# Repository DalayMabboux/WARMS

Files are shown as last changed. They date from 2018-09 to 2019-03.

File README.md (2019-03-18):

# WARMS
> Automatic plant watering with remote control and luminance, temperature and humidity data logging

Measures the moisture levels with two sensors and waters the plants individually.
The values are transmitted from the ESP8266 over MQTT to Node-RED, If the moisture level is too low the ESP8266 will be instructed to switch on the micro water pumps.

WARMS (http://www.youtube.com/watch?v=PIqeCujVt_k "WARMS")

## Overview
The whole installation consists of the following parts:
1. A Raspberry PI running Mosquitto (MQTT server) and Node-RED
2. A sensor box made up from a ESP8266, some sensors, micro pumps, etc.
3. A cloud based (GKE Google Kubernetes Engin) watchdog. If the cloud 'alive' doesn't get a callback from Node-RED, then an email will be sent . If the cloud 'alive' doesn't get a callback from Node-RED, then an email ("Alert, no heartbeat recevied from WARMS") will be sent.

## Raspberry PI
### SSL certificate
As the sensor data and the modification of the watering trigger value should easily be changeable, the Node-RED UI will be reachable over the Internet.
And secure it accordingly we'll enable HTTPS.
With the free service from [Let’s Encrypt](https://letsencrypt.org/) this is an easy task.
1) Get a certificate for madalito.internet-box.ch: `sudo certbot certonly --standalone --preferred-challenges http-01 -d madalito.internet-box.ch`
   * Hint: Create a cron job trying every hour to get a certificate
   
1) Also add a cron job to renew the certificate: `0 3 * * 6 certbot renew --noninteractive --standalone --post-hook "systemctl restart mosquitto"`

See [here](https://www.digitalocean.com/community/tutorials/how-to-install-and-secure-the-mosquitto-mqtt-messaging-broker-on-ubuntu-16-04) for a good info page.

### Node-RED
1) Follow the installation instruction on the [Node-RED site (Raspberry PI)](https://nodered.org/docs/hardware/raspberrypi).
1) Install [node-red-dashboard](https://github.com/node-red/node-red-dashboard)
1) Copy / paste [this](code/NodeRED.json)

#### Dashboard
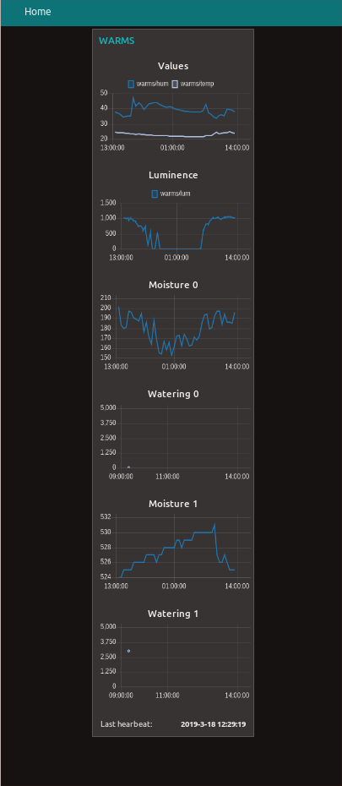
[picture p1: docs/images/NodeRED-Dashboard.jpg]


### Mosquitto
1) Install mosquitto
1) Configure mosquitto:
   - Don't allow anonymous access
   - Specify the location of the SSL certificate
   - Configuration: [default.conf](code/default.conf) [mosquitto.conf](code/mosquitto.conf)
1) Restart: `sudo systemctl restart mosquitto`

## Sensor box
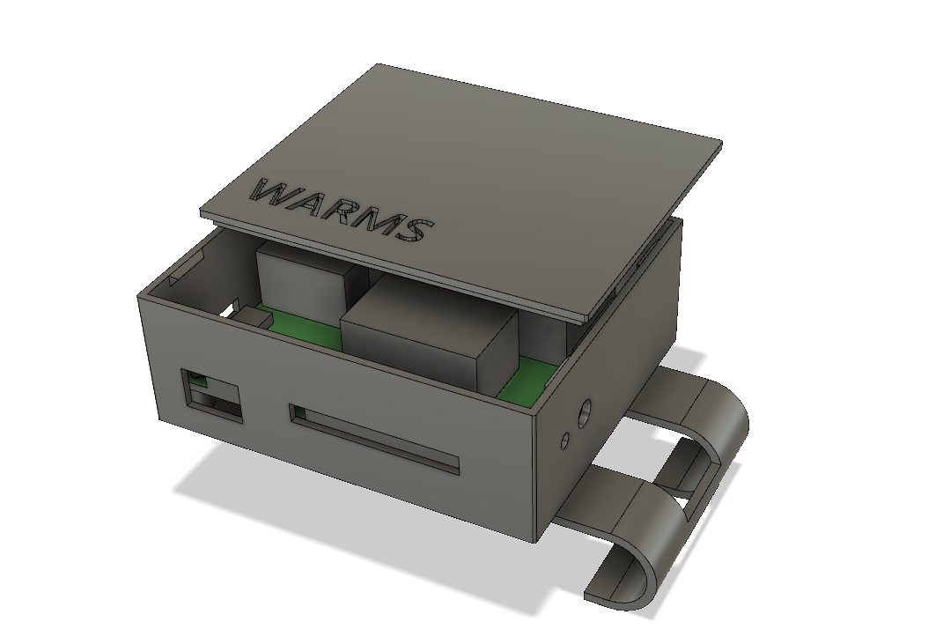
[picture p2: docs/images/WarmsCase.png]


### Printed circuit
For the first prototype I used an `Arduino Nano` and an ESP8266 to connect to the Internet. The Arduino was wired to the ESP8266 by a software serial connection. I wasn't able to build a reliable link between the two. So I dropped the Arduino an used just the ESP8266. The only issue with this approach was, that the ESP8266 (ESP-01) didn't have enough IO ports (one less I needed) available.
Fortunately there is a [solution](https://www.instructables.com/id/More-GPIO-for-ESP8266-01/) to this problem :)

[JLCPCB](https://jlcpcb.com) printed 10 of them for 2$ (exclusive shipping costs).

#### Schema
The schema has been drawn in [Autodesk EAGLE](https://www.autodesk.com/products/eagle/overview).

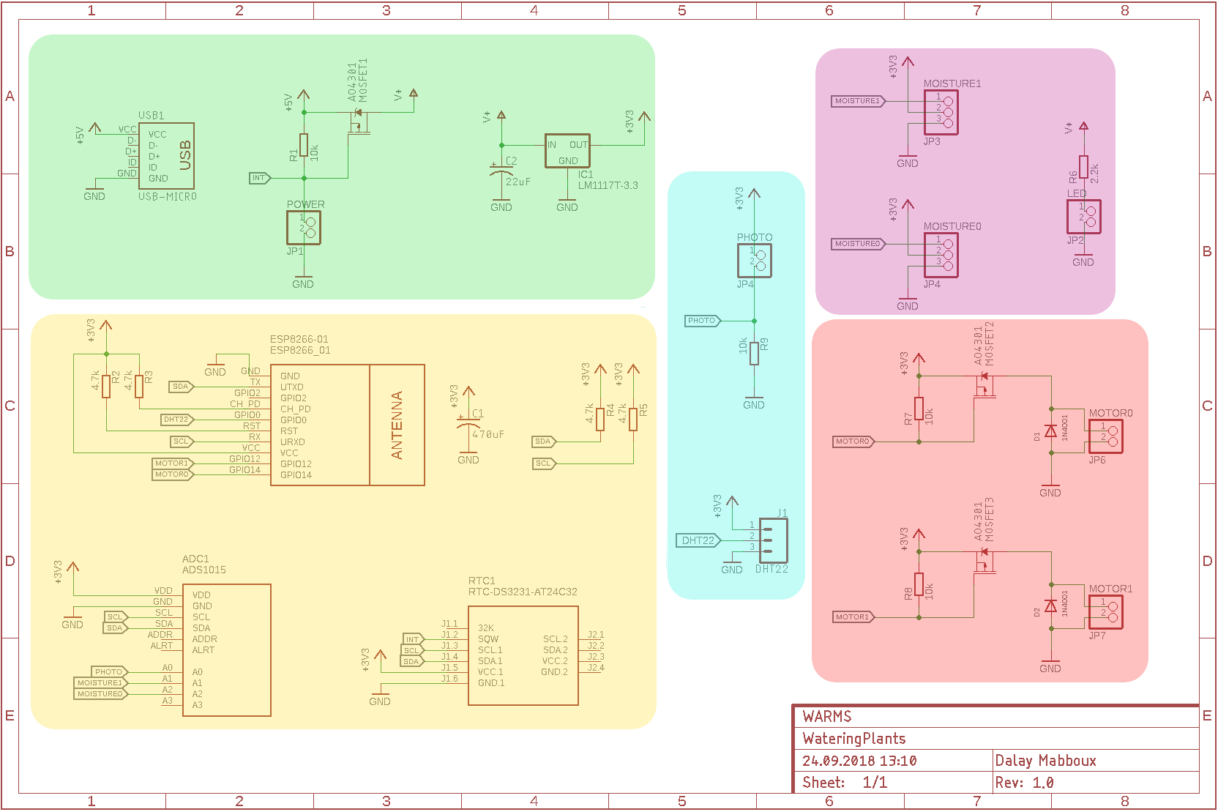
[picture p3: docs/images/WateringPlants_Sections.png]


It is grouped into these sectios:
Color | Section | Remark
--- | --- | ---
Green | Power supply | USB connector, 5V to 3.3V converter and switching circuit
Yellow | Micro-controller and sensor circuits | 
Blue | Sensor connectors | Moisture, luminance, etc
Purple | Green power led | Switches on once the device is running
Red | Water pump driver |

> The device will be powered off until the DS3231 switches SQW low (interrupt output). This happens when a set alarm occurs (currently it is set to 30min).
> If `INT` is low then VGS will be greater than VGS threshold and the P-Channel MOSFET turns on. Then the voltage on V+ will be ~5V and with LM 1117T-3.3 will output 3.3V. The ESP8266 boots and starts the sketch (todo: see).

##### Power supply (green)
Most of the functionality has already been described in the paragraph above.

The POWER jumper JP1 is used to manually boot the device. Needed, when you first start the board (as no alarm is set at this time).

##### Micro controller and sensor circuits (yellow)
The Real-Time-Clock (RTC-DS3231) and the Analog-to-Digital converter (ADS1015) are connected to the ESP8266 by I2C.

C1 is used as decoupling capacitor (I really had weird phenomenon without it).

As the ESP8266-01 just has 2 GPIO's (GPIO 0 and GPIO 2) and these have special purpose functionality while the the micro controller starts. I decided to wire out GPIO 12 and GPIO 14 to get some extra unused pins. If I didn't already have these boards I would by another version of the ESP8266 (ex. ESP-07) to circumvent the tinkering / soldering (see [here](https://www.instructables.com/id/More-GPIO-for-ESP8266-01/) how to do it).

The WARMS board just uses 3 (A0 to A3) of the 4 AD inputs of the ADS1015.

##### Water pump driver (red)
MOTOR0 and MOTOR1 will be set to GND to switch on the P-channel MOSFETS.

The diodes (D1 and D2) are just Flyback-Diodes.

#### Arduino sketch
The sketch first sets all parts up (I2C, RTC, Wifi, MQTT, IN-OUTPUT). Then the main loop starts by connecting to MQTT (subscribe for PUMP and SLEEP messages). The SLEEP functionallity hasn't yet been implemented.
Once all is set up, then it starts transmitting the luminence, moisture 1 and 2, humidity and temparture.

### 3D printed parts
All parts have been drawn with [Autodesk Fusion 360](https://www.autodesk.com/products/fusion-360/overview).
The Fusion Archive file can be found [here](code/WARMS_Box.f3d).

## Meta
Dalay Mabboux – [@mabbouxd](https://twitter.com/mabbouxd)

WARMS is licensed under a
Creative Commons Attribution-ShareAlike 4.0 International License.

You should have received a copy of the license along with this
work. If not, see <http://creativecommons.org/licenses/by-sa/4.0/>.

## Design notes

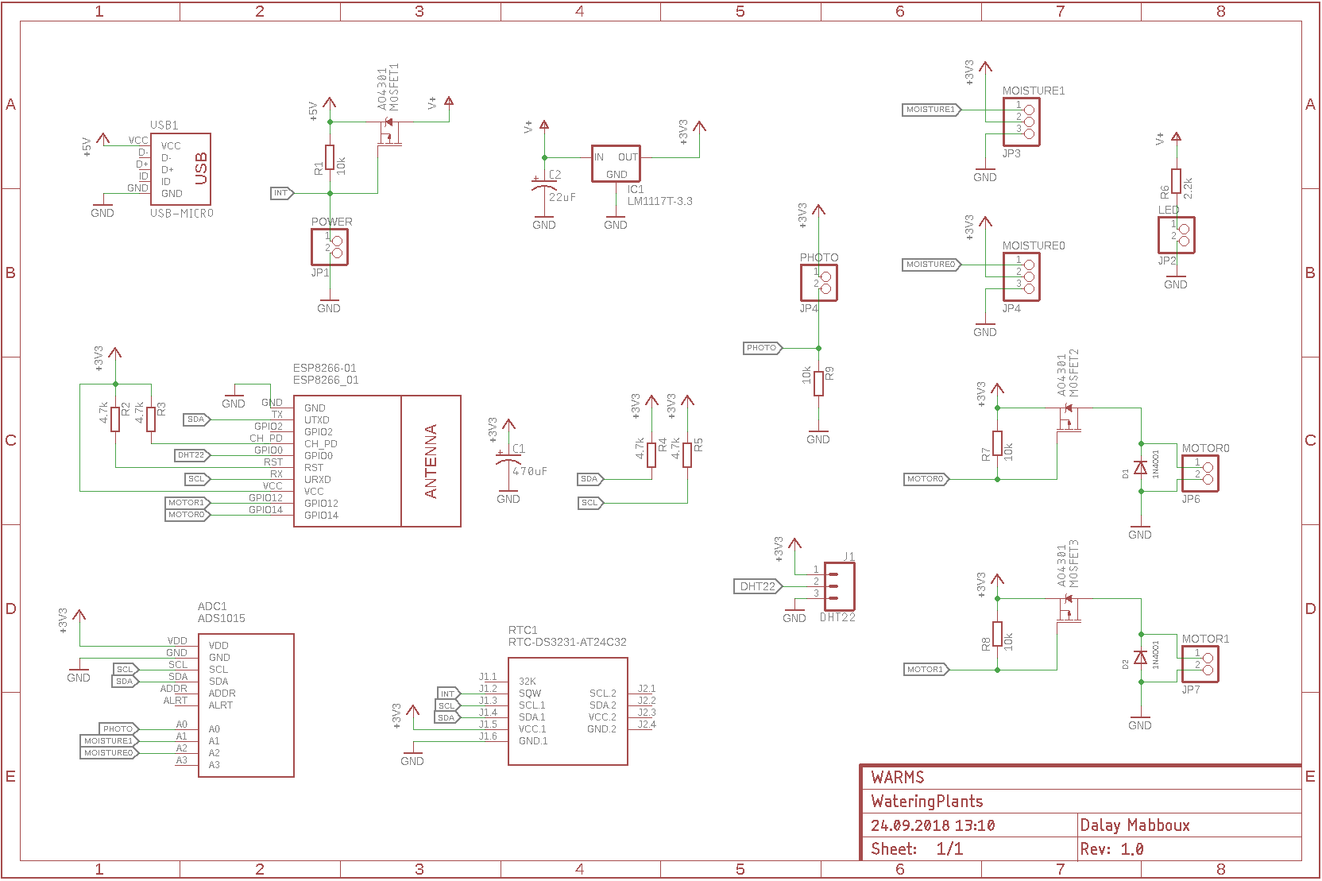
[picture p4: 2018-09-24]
docs/images/WateringPlants.png

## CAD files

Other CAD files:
code/WARMS_Box.f3d

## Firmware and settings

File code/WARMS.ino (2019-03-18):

/*
WARMS (c) by Dalay Mabboux

WARMS is licensed under a
Creative Commons Attribution-ShareAlike 4.0 International License.

You should have received a copy of the license along with this
work. If not, see <http://creativecommons.org/licenses/by-sa/4.0/>.
*/

#include <ESP8266WiFi.h>
#include <ESP8266WiFiMulti.h>
#include <PubSubClient.h>
#include <Wire.h> // must be included here so that Arduino library object file references work
#include <RtcDS3231.h>
#include <Adafruit_ADS1015.h>
#include "DHT.h"

// GPIO
const short int DHTPIN = 0; // GPIO0
const short int PUMP0 = 14; //GPIO14
const short int PUMP1 = 12; //GPIO12

// DIV
short int LL = 2; // Log level: 2 = debug, 1 = info, 0 = failure
short int sleepDuration = 1800; // Measurement period, default = 30min = 1800s
bool callbackHandled = false;

// MQTT
const char MQTT_SERVER[] =    "1.1.1.1";
const int MQTT_SERVERPORT =   1883;
const char MQTT_USERNAME[] =  "warms";
const char MQTT_PASSWORD[] =  "xxxxxxxxxx";
const char* MQTT_USERID;

// Feeds
const char MQTT_FEED_LOG[] =  "warms/log";
const char MQTT_FEED_TEMP[] = "warms/temp";
const char MQTT_FEED_HUM[] =  "warms/hum";
const char MQTT_FEED_LUM[] =  "warms/lum";
const char MQTT_FEED_MOI0[] = "warms/moi0";
const char MQTT_FEED_MOI1[] = "warms/moi1";
// Subscriptions
const char MQTT_SUB_PUMPS[] = "warms/pumps";
const char MQTT_SUB_SLEEP[] = "warms/sleepDuration";

// WIFI
const char WIFI_SSID[] = "xxxxxxxxxx";
const char WIFI_PASSWORD[] = "xxxxxxxxxx";
ESP8266WiFiMulti WiFiMulti;
WiFiClient wclient;
PubSubClient mqttclient(wclient);

// AD-Converter
Adafruit_ADS1015 ads;

// RTC
RtcDS3231<TwoWire> rtc(Wire);
#define countof(a) (sizeof(a) / sizeof(a[0]))

// DHT
const uint8_t DHTTYPE = DHT22;
DHT dht(DHTPIN, DHTTYPE);

struct PUMP_DURATIONS {
  unsigned int p0;
  unsigned int p1;
};

PUMP_DURATIONS calcPumpDurations(byte* payload);


/* SETUP ************************************************************************************************/
void setup() {
  Wire.begin(1, 3);
  rtc.Begin();
  rtc.Enable32kHzPin(false);
  rtc.SetSquareWavePin(DS3231SquareWavePin_ModeAlarmOne);
  ads.begin();
  dht.begin();

  RtcDateTime compiled = RtcDateTime(__DATE__, __TIME__);
  RtcDateTime now = rtc.GetDateTime();
  rtc.SetDateTime(compiled);

  if (!rtc.GetIsRunning()) {
    rtc.SetIsRunning(true);
  }

  // WIFI
  WiFi.mode(WIFI_STA);
  WiFiMulti.addAP(WIFI_SSID, WIFI_PASSWORD);
  while (WiFiMulti.run() != WL_CONNECTED) { // Wait until WIFI has been connected
    delay(500);
  }

  // MQTT
  String clientId = "ESP8266Client-";
  clientId += String(random(0xffff), HEX);
  MQTT_USERID = clientId.c_str();
  mqttclient.setServer(MQTT_SERVER, 1883);
  mqttclient.setCallback(callback);

  // PINMODES
  pinMode(PUMP0, OUTPUT);
  digitalWrite(PUMP0, HIGH);
  pinMode(PUMP1, OUTPUT);
  digitalWrite(PUMP1, HIGH);
}

/* LOOP ************************************************************************************************/
void loop() {
  if (!mqttclient.connected()) {
    if (mqttclient.connect(MQTT_USERID, MQTT_USERNAME, MQTT_PASSWORD)) {
      mqttclient.subscribe(MQTT_SUB_PUMPS);
      mqttclient.subscribe(MQTT_SUB_SLEEP);
    }
  }
  
  if (!callbackHandled) {
    if (mqttclient.connected()) {
      // Check RTC
      if (!rtc.IsDateTimeValid()) {
        log2mqtt(0, "RTC date/time is not valid (IsDateTimeValid() == false");
      }
      if (!rtc.GetIsRunning()) {
        log2mqtt(0, "RTC was not actively running, starting now");
        rtc.SetIsRunning(true);
      } 
  
      // Handle moisture 1 sensor
      int16_t adc0 = ads.readADC_SingleEnded(0);
      publishFloat(MQTT_FEED_LUM, (float)adc0);
  
      // Handle moisture 2 sensor
      int16_t adc1 = ads.readADC_SingleEnded(1);
      publishFloat(MQTT_FEED_MOI0, (float)adc1);
  
      // Handle light sensor
      int16_t adc2 = ads.readADC_SingleEnded(2);
      publishFloat(MQTT_FEED_MOI1, (float)adc2);
  
      // DHT
      float dhtTemp = dht.readTemperature();
      float dhtHum = dht.readHumidity();
      publishFloat(MQTT_FEED_HUM, dhtHum);
      publishFloat(MQTT_FEED_TEMP, dhtTemp);
  
      // Wait one minute in total for a callback
      int mqttLoops = 12;
      while(mqttLoops >= 0) {
        mqttclient.loop();
        delay(5000);
        --mqttLoops;
      }
    }
  }
  
  // Set alarm
  RtcDateTime now = rtc.GetDateTime();
  RtcDateTime alarmTime = now + sleepDuration;
  DS3231AlarmOne alarm1(alarmTime.Day(), alarmTime.Hour(), alarmTime.Minute(), alarmTime.Second(), DS3231AlarmOneControl_HoursMinutesSecondsMatch);
  char tmpString[150];
  sprintf(tmpString, "Alarm set: %u-%u-%u %u:%u:%u", alarmTime.Year(), alarmTime.Month(), alarmTime.Day(), alarmTime.Hour(), alarmTime.Minute(), alarmTime.Second());
  log2mqtt(2, tmpString);
  // Wait a couple of seconds to send the log entry
  delay(5000);
  rtc.SetAlarmOne(alarm1);
  // Next command will power off the board
  rtc.LatchAlarmsTriggeredFlags();
}

/*
  Publishes the given string to the log feed if the specified loglevel is lower or equal to the log level (LL).
  Max. string size = 80 characters.
  ------------------------------------------------------------------------------------------------------------
    l:    the log level
    m:    the string to send to the log feed

    returns: void
*/
void log2mqtt(short int l, char m[]) {
  if (l <= LL) {
    mqttclient.publish(MQTT_FEED_LOG, m);
  }
}

/* Publishes the float val to the given topic. Format: YYY.YY */
void publishFloat(char const topic[], float val) {
  char tmp[7];
  dtostrf(val, 5, 2, tmp);
  mqttclient.publish(topic, tmp);
}

/* Called when receiving a message from MQTT broker */
void callback(char* topic, byte* payload, unsigned int length) {
  // In order to republish this payload, a copy must be made
  // as the orignal payload buffer will be overwritten whilst
  // constructing the PUBLISH packet.
  byte* p = (byte*) malloc(length);
  memcpy(p, payload, length);

  char tmpString[150];
  sprintf(tmpString, "Received message for the topic '%s' with the payload '%s'", topic, p);
  log2mqtt(2, tmpString);
  
  if (strcmp(topic, MQTT_SUB_SLEEP) == 0) {
    sleepDuration = atoi((char*)p);
    sprintf(tmpString, "Sleep duration set to '%u'", sleepDuration);
    log2mqtt(1, tmpString);
  } else if (strcmp(topic, MQTT_SUB_PUMPS) == 0) {
    PUMP_DURATIONS pumpWateringDurations = calcPumpDurations(p);
    sprintf(tmpString,  "Watering: pump 0 for '%u' [ms] and pump 1 for '%u' [ms]", pumpWateringDurations.p0, pumpWateringDurations.p1);
    log2mqtt(1, tmpString);
    if (pumpWateringDurations.p0 > 0) {
      pump(PUMP0, pumpWateringDurations.p0);
    }
    if (pumpWateringDurations.p1 > 0) {
      pump(PUMP1, pumpWateringDurations.p1);
    }
  } else {
    sprintf(tmpString, "Unknown topic '%s'", topic);
    log2mqtt(1, tmpString);
  }
  free(p);
  callbackHandled = true;
}

/*
   Extracts from the payload the first 8 characters, splits it in two strings, converts them into 'unsignged int' and returns them as a pointer.
*/
PUMP_DURATIONS calcPumpDurations(byte* payload) {
  char mot0[5];
  char mot1[5];
  // Get first 4 characters and convert them
  strncpy(mot0, (char*)payload, 4);
  mot0[4] = '\0';
  // Get the next 4 characters and convert them
  strncpy(mot1, (char*)payload + 4, 4);
  mot1[4] = '\0';
  //unsigned int t[] = {atoi(mot0), atoi(mot1)};
  return (PUMP_DURATIONS) {
    atoi(mot0), atoi(mot1)
  };
}

/*
   Activates the given pump for the specified duration.
   ----------------------------------------------------
    pump: the pump to activate (0 or 1)

*/
void pump(unsigned int pump, unsigned long duration) {
  digitalWrite(pump, LOW);
  delay(duration);
  digitalWrite(pump, HIGH);
}
